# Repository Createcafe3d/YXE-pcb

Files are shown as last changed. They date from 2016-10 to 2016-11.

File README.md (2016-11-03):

Big thanks to Rylan @Peachy for opensourcing the entire project.

Peachy Printer was gearing up to manufacture the mini-v1.14 board. If you're wondering what v1.15 is all about, it's a work-in-progress that we started because of a huge panic: right around the time we were getting ready for our final test manufacturing run, the STM32F042 practically vanished from the entire supply chain! We couldn't find them anywhere! So I quickly started redoing the board to use an STM32F070 instead, but in the end the supply chain recovered before we had to pull the trigger on the respin.

**Todos:**
- Create the trans impedence amplifier for the laser sense pin.
  - This lets us tune the laser power to the "draw velocity" - making for nicer cornering and faster printing
  - The sense pin on the laser is currently grounded (and wrongly labeled as "Laser-EN")

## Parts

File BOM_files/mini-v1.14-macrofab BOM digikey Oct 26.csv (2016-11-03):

Qty | Value | Device | DK P/N | Extended | DK for Ext$ | Package | DK Order Oct 26 | Boards Oct 26
13 | 100n | CAPACITOR_NP_0603 | 399-1095-2-ND | 65000 | 362.7 | C0603 | 4000 | 307
1 | 10uF | CAPACITOR_P_4MM | 490-7201-2-ND | 5000 | 484.35 | CP4MM | 250 | 250
5 | 1uF | C-USC0603 | 311-1443-2-ND | 25000 | 178.25 | C0603 | 4000 | 800
1 | 560pF/50V | C-USC0603 | 1276-1278-2-ND | 5000 | 62.9 | C0603 | 4000 | 4000
1 | BAT42 | DIODE_SOD-123 | BAT42W-FDITR-ND | 5000 | 442.2 | SOD-123 | 120 | 120
4 |  | LEDCHIP-LED0603 | 475-2512-2-ND | 20000 | 1071.2 | CHIP-LED0603 | 1000 | 250
5 | LMC7101 | LMC7101 | 576-2575-2-ND | 25000 | 7725.5 | SOT23-5 | 600 | 120
1 | LMR62014 | LMR62014 | 296-39046-2-ND | 5000 | 2595.55 | SOT23-5 | 120 | 120
1 | ferrite | L-US |  | 5000 |  | C0603 |  | 0
1 | MBR0520 | MBR0520 | MBR0520LT1GOSTR-ND | 5000 | 397.2 | SOD123 | 120 | 120
2 | SMF6.0A | MBR0520 | F5749TR-ND | 10000 | 1517.1 | SOD123 | 250 | 125
2 | NC7WZ14P6X | NC7WZ14P6X | NC7WZ14P6XTR-ND | 10000 | 810.4 | SC70-6 | 250 | 125
2 | BSS138 | N-CHANNEL_FET_SOT-23-3 | BSS138LT3GOSTR-ND | 10000 | 451.64 | SOT-23-3 | 240 | 120
3 |  | PINHD-2X3 | 952-1921-ND | 15000 | 2617.5 | 2X03 | 360 | 120
2 | 10 | RESISTOR_0603 | 311-10.0HRTR-ND | 10000 | 21.26 | R0603 | 5000 | 2500
1 | 100k | RESISTOR_0603 | 311-100KHRTR-ND | 5000 | 9.62 | R0603 | 5000 | 5000
2 | 13k3 | RESISTOR_0603 | 311-13.3KHRTR-ND | 10000 | 21.26 | R0603 | 5000 | 2500
5 | 1k69 | RESISTOR_0603 | 311-1.69KHRTR-ND | 25000 | 47.5 | R0603 | 5000 | 1000
16 | 2k | RESISTOR_0603 | 311-2.00KHRTR-ND | 80000 | 139.2 | R0603 | 5000 | 312
5 | 604k | RESISTOR_0603 | 311-604KHRTR-ND | 25000 | 47.5 | R0603 | 5000 | 1000
1 | 63k4 | RESISTOR_0603 | 311-63.4KHRTR-ND | 5000 | 12.45 | R0603 | 5000 | 5000
10 | 825k | RESISTOR_0603 | 311-825KHRTR-ND | 50000 | 21.62 | R0603 | 5000 | 500
1 | SDR0403-100ML | SDR0403 | SDR0403-100MLTR-ND | 5000 | 1287.25 | SDR0403 | 120 | 120
1 | SP3002-04JTG | SP3002 | F2916TR-ND | 5000 | 1824.75 | SC70-6 | 120 | 120
1 | STM32F070CBT6 | STM32F042-LQFP48 | 497-15099-ND | 5000 | 8179.93 | LQFP48 | 120 | 120
1 | TLV70233PDBVR | TLV70233PDBVR | 296-39284-2-ND | 5000 | 767.64 | SOT-23-5 | 120 | 120
1 |  | USB_MICRO_RIGHT | 609-4618-2-ND | 5000 | 1258.45 | MICROUSB-RIGHT | 120 | 120
TOTAL |  |  |  |  | 32354.92
PER BOARD |  |  |  |  | 6.470984

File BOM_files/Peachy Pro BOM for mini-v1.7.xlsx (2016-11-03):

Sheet: Ordering
Value | Device | Package | Digikey Part | Newark Part Number | Unit Price | /1000 price | QTY | Single Price | Vol Price | QTY +15%
100n | C-USC0603 | C0603 | 399-1095-1-ND |  | 0.13 | 0.00816 | 5 | 0.65 | 0.0408 | 58
10n | C-USC0603 | C0603 | 399-8988-1-ND |  | 0.32 | 0.06934 | 1 | 0.32 | 0.06934 | 12
10uF | C-USC0603 | C0603 | 490-10475-1-ND |  | 0.27 | 0.05056 | 1 | 0.27 | 0.05056 | 12
1u | C-USC0603 | C0603 | 587-1242-1-ND |  | 0.13 | 0.01321 | 3 | 0.39 | 0.03963 | 35
2.2u | C-USC0603 | C0603 | 587-2983-1-ND |  | 0.22 | 0.04095 | 1 | 0.22 | 0.04095 | 12
4.7n | C-USC0603 | C0603 | 399-1087-1-ND |  | 0.13 | 0.00971 | 4 | 0.52 | 0.03884 | 46
470n | C-USC0603 | C0603 | 587-1252-1-ND |  | 0.13 | 0.02136 | 4 | 0.52 | 0.08544 | 46
470p | C-USC0603 | C0603 | 399-1075-1-ND |  | 0.13 | 0.01398 | 1 | 0.13 | 0.01398 | 12
560pF/50V | C-USC0603 | C0603 | 399-1076-1-ND |  | 0.32 | 0.07911 | 1 | 0.32 | 0.07911 | 12
820n | C-USC0603 | C0603 | 399-3117-1-ND |  | 0.34 | 0.08216 | 1 | 0.34 | 0.08216 | 12
BAT60A | BAT60A | SOD323 | BAT60AE6327INCT-ND |  | 0.71 | 0.14888 | 2 | 1.42 | 0.29776 | 23
74S04D | 74S04D | SO14 | 568-1384-1-ND |  | 0.63 | 0.13336 | 1 | 0.63 | 0.13336 | 12
 | LEDCHIP-LED0603 | CHIP-LED0603 | 475-2512-1-ND |  | 0.12 | 0.06086 | 4 | 0.48 | 0.24344 | 46
IRLR3105TR | FET-N-IRLR3105TRIRLR3105TR | DPAK | IRLR3105TRPBFCT-ND |  | 1.48 | 0.5535 | 1 | 1.48 | 0.5535 | 12
1 | R-US_R0603 | R0603 | 541-1.00HHCT-ND |  | 0.112 | 0.02359 | 1 | 0.112 | 0.02359 | 12
100 | R-US_R0603 | R0603 | 541-100HCT-ND |  | 0.112 | 0.02359 | 1 | 0.112 | 0.02359 | 12
100k | R-US_R0603 | R0603 | 541-100KHCT-ND |  | 0.112 | 0.02359 | 1 | 0.112 | 0.02359 | 12
10k | R-US_R0603 | R0603 | 541-10.0KHCT-ND |  | 0.112 | 0.02359 | 1 | 0.112 | 0.02359 | 12
13k3 | R-US_R0603 | R0603 | 541-13.3KHCT-ND |  | 0.112 | 0.02359 | 1 | 0.112 | 0.02359 | 12
1k | R-US_R0603 | R0603 | 541-1.00KHCT-ND |  | 0.112 | 0.02359 | 2 | 0.224 | 0.04718 | 23
1M | R-US_R0603 | R0603 | 541-1.00MHCT-ND |  | 0.112 | 0.02359 | 5 | 0.56 | 0.11795 | 58
3k9 | R-US_R0603 | R0603 | 541-3.90KHCT-ND |  | 0.112 | 0.02359 | 4 | 0.448 | 0.09436 | 46
52k3 | R-US_R0603 | R0603 | 541-52.3KHCT-ND |  | 0.112 | 0.02359 | 1 | 0.112 | 0.02359 | 12
9k9 | R-US_R0603 | R0603 | 541-9.09KHCT-N |  | 0.112 | 0.02359 | 1 | 0.112 | 0.02359 | 12
LD3985M33R | LD3985MXXR | SOT23-5L | 497-3504-1-ND |  | 0.96 | 0.33535 | 1 | 0.96 | 0.33535 | 12
 | R-US_R0603 | R0603 | 541-1.00KHCT-ND |  | 0.112 | 0.02359 | 4 | 0.448 | 0.09436 | 46
FCI-MICRO-USB | FCI-MICRO-USB | FCI-MICROUSB | 609-4613-1-ND |  | 0.6 | 0.3365 | 1 | 0.6 | 0.3365 | 12
LMC7101 | LMC7101 | SOT23-5 | 576-2575-1-ND |  | 0.98 | 0.389 | 4 | 3.92 | 1.556 | 46
LMH6645MF | OPAMP-SINGLELMH6645MF | SOT23-5 | LMH6645MF/NOPBCT-ND |  | 2.49 | 0.97596 | 1 | 2.49 | 0.97596 | 12
LMR62014 | LMR62014 | SOT23-5 | LMR62014XMF/NOPBCT-ND |  | 2.32 | 0.80116 | 1 | 2.32 | 0.80116 | 12
MBR0520 | MBR0520 | SOD123 | MBR0520LT1GOSCT-ND | 48K7498 | 0.407 | 0.076 | 3 | 1.221 | 0.228 | 35
SDR0403-100ML | SDR0403 | SDR0403 | SDR0403-100MLCT-ND |  | 0.65 | 0.31547 | 1 | 0.65 | 0.31547 | 12
SP3002 | SP3002 | SC70-6 | F2916CT-ND |  | 0.96 | 0.38456 | 2 | 1.92 | 0.76912 | 23
STM32F042-LQFP48 | STM32F042-LQFP48 | LQFP48 | 497-14648-ND |  | 4.08 | 2.04112 | 1 | 4.08 | 2.04112 | 12
 | L_TDK_1005 | MLK1005 | 445-1565-1-ND |  | 0.13 | 0.03518 | 1 | 0.13 | 0.03518 | 12
 | NOTE: Replace the existing one with this one (0603)
 |  |  |  |  |  |  | 68 | 28.445 | 9.68171

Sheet: Assembly
Value | QTY | x3
100n | 5 | 15
10n | 1 | 3
10uF | 1 | 3
1u | 3 | 9
2.2u | 1 | 3
4.7n | 4 | 12
470n | 4 | 12
470p | 1 | 3
560pF/50V | 1 | 3
820n | 1 | 3
BAT60A | 2 | 6
74S04D | 1 | 3
 | 4 | 12
IRLR3105TR | 1 | 3
1 | 1 | 3
100 | 1 | 3
100k | 1 | 3
10k | 1 | 3
13k3 | 1 | 3
1k | 2 | 6
1M | 5 | 15
3k9 | 4 | 12
52k3 | 1 | 3
9k9 | 1 | 3
LD3985M33R | 1 | 3
 | 4 | 12
FCI-MICRO-USB | 1 | 3
LMC7101 | 4 | 12
LMH6645MF | 1 | 3
LMR62014 | 1 | 3
MBR0520 | 3 | 9
SDR0403-100ML | 1 | 3
SP3002 | 2 | 6
STM32F042-LQFP48 | 1 | 3
 | 1
 | 68

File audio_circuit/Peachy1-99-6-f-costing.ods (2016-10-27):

Qty | Value | Device | Package | Parts | Description | BOM | DIGIKEY | MF | MPN | Price @500 | Ext @500 | Price @5000 | Ext @5000
1 | 200R | TRIM_US-PVZ3A | PVZ3A | VR5 | POTENTIOMETER |  |  |  | PVZ3G331C01R00 ??? (in stock, not the right one though) | 0.1359 | 0.1359 | 0.12063 | 0.12063
1 | FCI-MICROUSBAPCIRCUITS | FCI-MICROUSBAPCIRCUITS | FCI-USB-10118193-APCIRCUITS | USB2 |  |  |  |  | 10118193-0001LF | 0.31476 | 0.31476 | 0.31476 | 0.31476
1 | LASERDIODELD2 | LASERDIODELD2 | LASERDIODE2 | LD1 |  |  |  |  | 3 x (0552-2-15-15-11-27-10-0) | 0.30582 | 0.30582 | 0.24144 | 0.24144
2 | 10k | TRIM_US-67W | 67W | VR1, VR2 | POTENTIOMETER |  |  |  | 67WR10KLF | 0.64435 | 1.2887 | 0.62981 | 1.25962
1 | ADP1613 | ADP1613 | RM-8 | U1 |  |  |  |  | ADP1613ARMZ-R7 | 1.44978 | 1.44978 | 1.04706 | 1.04706
1 | ADP2300 | ADP2300 | TSOT23-6 | U2 | Nonsynchronous Step-Down Regulator |  |  |  | ADP2300AUJZ-R7 | 1.6776 | 1.6776 | 1.2582 | 1.2582
1 | BC857CT | BC857CT | SC-75 | Q3 |  |  |  |  | BC857CT,115 | 0.0748 | 0.0748 | 0.04457 | 0.04457
1 | MM3ZST1G | MM3ZST1G | SOD323-R | ZD1 |  |  |  |  | BZX384-B3V3,115 | 0.09586 | 0.09586 | 0.05711 | 0.05711
2 | 4.7uF | C-US0805 | C0805 | CIN, CIN-NEG | CAPACITOR, American symbol |  |  |  | CL21A475KOFNNNE | 0.03198 | 0.06396 | 0.02326 | 0.04652
3 | 0.01uF | C-US0805 | C0805 | C4, C6, CSS | CAPACITOR, American symbol |  |  |  | CL21B103KBANNNC | 0.00941 | 0.02823 | 0.00627 | 0.01881
3 | 0.1uF | C-US0805 | C0805 | C1, C2, C3 | CAPACITOR, American symbol |  | 1276-1099-2-ND |  | CL21B104KACNNNC | 0.01344 | 0.04032 | 0.00896 | 0.02688
2 | 0.1uF | C-US0805 | C0805 | C11, CBST-NEG | CAPACITOR, American symbol |  | 1276-1099-2-ND |  | CL21B104KACNNNC | 0.01344 | 0.02688 | 0.00896 | 0.01792
4 | 1uF | C-US0805 | C0805 | C8, C9, CC-NEG, CV5 | CAPACITOR, American symbol |  |  |  | CL21B105KBFNNNE | 0.01802 | 0.07208 | 0.01441 | 0.05764
2 | 10uF | C-US0805 | C0805 | COUT1, COUT1-NEG | CAPACITOR, American symbol |  |  |  | CL21B106KQQNNNE | 0.06856 | 0.13712 | 0.05109 | 0.10218
1 | 6800pF | C-US0805 | C0805 | CC1 | CAPACITOR, American symbol |  |  |  | CL21B682KBANNNC | 0.02016 | 0.02016 | 0.01203 | 0.01203
1 | 10pF | C-US0805 | C0805 | CC2 | CAPACITOR, American symbol |  |  |  | CL21C100JCANNNC | 0.00688 | 0.00688 | 0.0115 | 0.0115
2 | DMG4406LSS | DMG4406LSS | SO8_DMG | Q1, Q2 |  |  |  |  | DMG4406LSS-13 | 0.13099 | 0.26198 | 0.1081 | 0.2162
3 | LM324ADR | LM324ADR | SOIC14(TI-PKG-D) | IC1, IC2, IC3 | OP AMP |  |  |  | LM324ADR | 0.13668 | 0.41004 | 0.10713 | 0.32139
2 | LMC7101 | LMC7101 | SOT23-5 | IC4, IC5 |  |  |  |  | LMC7101BYM5 | 0.36393 | 0.72786 | 0.28075 | 0.5615
1 | 4.7uH | L-USL1210 | L1210 | L1 | INDUCTOR, American symbol |  |  |  | LQH32PN4R7NN0L | 0.28854 | 0.28854 | 0.17212 | 0.17212
1 | 6.8uH | L-USL1210 | L1210 | L1-NEG | INDUCTOR, American symbol |  |  |  | LQH32PN6R8NN0 | 0.28854 | 0.28854 | 0.17212 | 0.17212
4 | RED | LEDCHIPLED_0603 | CHIPLED_0603 | LED1, LED2, LED3, LED4 | LED |  |  |  | LS L29K-G1J2-1-Z | 0.1107 | 0.4428 | 0.09203 | 0.36812
2 | MBR0520 | SCHOTTKYSOD123 | SOD123 | D1-NEG, D3 |  |  |  |  | MBR0520LT3G | 0.07836 | 0.15672 | 0.05065 | 0.1013
1 | MMBT3904 | MMBT3904 | SOT23 | Q4 |  |  |  |  | MMBT3904,215 | 0.03678 | 0.03678 | 0.02069 | 0.02069
1 | OSTTE030104 | OSTTE030104 | OSTTE030104 | X6 |  |  |  |  | OSTTE030104 | 0.35318 | 0.35318 | 0.26488 | 0.26488
1 | 680k* | R-US_SOCKET(.1) | 70543-02 | R28 | RESISTOR, American symbol |  |  |  | PPTC021LFBN-RC | 0.22322 | 0.22322 | 0.15861 | 0.15861
2 | 10k | TRIM_US-PVZ3A | PVZ3A | VR3, VR4 | POTENTIOMETER |  |  |  | PVZ3A103C01R00 | 0.12911 | 0.25822 | 0.08966 | 0.17932
3 | RB751V40 | RB751V40 | SOD323-R | D1, D2, D4 |  |  |  |  | RB751V40,115 | 0.06435 | 0.19305 | 0.04159 | 0.12477
1 | 13k 1% | R-US_R0805 | R0805 | RF2-NEG | RESISTOR, American symbol |  |  |  | RC0805FR-0713KL | 0.00662 | 0.00662 | 0.00319 | 0.00319
2 | 1k37 1% | R-US_R0805 | R0805 | R8, R11 | RESISTOR, American symbol |  |  |  | RC0805FR-071K37L | 0.00489 | 0.00978 | 0.00277 | 0.00554
1 | 1K58 | R-US_R0805 | R0805 | R31 | RESISTOR, American symbol |  |  |  | RC0805FR-071K58L | 0.00662 | 0.00662 | 0.00319 | 0.00319
2 | 2k55 1% | R-US_R0805 | R0805 | R4, R12 | RESISTOR, American symbol |  |  |  | RC0805FR-072K55L | 0.00662 | 0.01324 | 0.00319 | 0.00638
1 | 3k9 1% | R-US_R0805 | R0805 | R13 | RESISTOR, American symbol |  |  |  | RC0805FR-073K9L | 0.00662 | 0.00662 | 0.00319 | 0.00319
1 | 41k2 | R-US_R0805 | R0805 | RF1 | RESISTOR, American symbol |  |  |  | RC0805FR-0741K2L | 0.00662 | 0.00662 | 0.00319 | 0.00319
5 | 6k8 1% | R-US_R0805 | R0805 | R14, R19, R20, R24, R25 | RESISTOR, American symbol |  |  |  | RC0805FR-076K8L | 0.00662 | 0.0331 | 0.00319 | 0.01595
1 | 84k5 1% | R-US_R0805 | R0805 | RF1-NEG | RESISTOR, American symbol |  |  |  | RC0805FR-0784K5L | 0.00662 | 0.00662 | 0.00319 | 0.00319
1 | 300R | R-US_R0805 | R0805 | R7 | RESISTOR, American symbol |  |  |  | RC0805JR-07300RL | 0.00572 | 0.00572 | 0.00274 | 0.00274
1 | 10k7 | R-US_R0805 | R0805 | RF2 | RESISTOR, American symbol |  |  |  | RC2012F1072CS | 0.00648 | 0.00648 | 0.00311 | 0.00311
1 | 1k2 | R-US_R0805 | R0805 | R17 | RESISTOR, American symbol |  |  |  | RC2012J122CS | 0.00562 | 0.00562 | 0.0027 | 0.0027
1 | 2k49 | R-US_R0805 | R0805 | RC1 | RESISTOR, American symbol |  |  |  | RMCF0805FT2K49 | 0.00866 | 0.00866 | 0.00343 | 0.00343
5 | 10k | R-US_R0805 | R0805 | R3, R21, R22, R30, REN | RESISTOR, American symbol |  |  |  | RMCF0805JT10K0 | 0.00348 | 0.0174 | 0.00213 | 0.01065
1 | 1R | R-US_R0805 | R0805 | RB0 | RESISTOR, American symbol |  |  |  | RMCF0805JT1R00 | 0.0062 | 0.0062 | 0.00245 | 0.00245
3 | 20k | R-US_R0805 | R0805 | R9, R10, R29 | RESISTOR, American symbol |  |  |  | RMCF0805JT20K0 | 0.00413 | 0.01239 | 0.00245 | 0.00735
4 | 220R | R-US_R0805 | R0805 | R16, R18, R23, R32 | RESISTOR, American symbol |  |  |  | RMCF0805JT220R | 0.00413 | 0.01652 | 0.00245 | 0.0098
6 | 470k | R-US_R0805 | R0805 | R5, R6, R26, R27, R35, R37 | RESISTOR, American symbol |  |  |  | RMCF0805JT470K | 0.00348 | 0.02088 | 0.00213 | 0.01278
4 | 47k | R-US_R0805 | R0805 | R1, R2, R34, R36 | RESISTOR, American symbol |  | RMCF0805JT47K0CT-ND |  | RMCF0805JT47K0 | 0.00348 | 0.01392 | 0.00213 | 0.00852
1 | 4R7 | R-US_R0805 | R0805 | R15 | RESISTOR, American symbol |  |  |  | RMCF0805JT4R70 | 0.0062 | 0.0062 | 0.00245 | 0.00245
1 | 560R* | R-US_R0805 | R0805 | R33 | RESISTOR, American symbol |  |  |  | RMCF0805JT560R | 0.0062 | 0.0062 | 0.00245 | 0.00245
2 | CUI-SJ-3523-SMT | CUI-SJ-3523-SMT | CUI-SJ-3523-SMT | CON1, CON2 |  |  |  |  | SJ-3523-SMT-TR | 0.62206 | 1.24412 | 0.49571 | 0.99142
2 | TSW-103-02-S-S | TSW-103-02-S-S | TSW-103-02-S-S | X7, X9 | THROUGH-HOLE .025" SQ POST HEADER |  |  |  | TSW-103-07-T-S | 0.30315 | 0.6063 | 0.26591 | 0.53182
3 |  | JUMPER-2SMD-NC | SJ_2S | JP1, JP2, JP3 | Jumper |  |  |  |  |  | 0 |  | 0
1 |  | JUMPER-2SMD-NO | SJ_2S-NO | X5 | Jumper |  |  |  |  |  | 0 |  | 0
2 | FIDUCIAL | FIDUCIAL | FIDUCIAL_1MM | U$2, U$3 | For use by pick and place machines to calibrate the vision/machine, 1mm |  |  |  |  |  | 0 |  | 0
2 | JUMPER-31-2 | JUMPER-31-2 | SJ_3_PASTE1&2 | X2, X3 |  |  |  |  |  |  | 0 |  | 0
1 | SHORT-HT5 | SHORT-HT5 | SHORT_TOP-50 | SH1 | Short between two nets | no |  |  |  |  | 0 |  | 0
15 | TP017HOLE | TP017HOLE | TP017TH | TP7, TP8, TP9, TP12, TP13, TP14, TP15, TP16, TP17, TP18, TP20, TP21, TP22, TP23, TP24 | Test pad |  |  |  |  |  | 0 |  | 0
1 | TP017HOLE | TP017HOLE | TP017TH | TP10 | Test pad |  |  |  |  |  | 0 |  | 0
1 | TP017HOLE | TP017HOLE | TP017TH | TP3 | Test pad |  |  |  |  |  | 0 |  | 0
1 | TP017HOLE | TP017HOLE | TP017TH | TP4 | Test pad |  |  |  |  |  | 0 |  | 0
1 | TP017HOLE | TP017HOLE | TP017TH | TP2 | Test pad |  |  |  |  |  | 0 |  | 0
1 | TP017HOLE | TP017HOLE | TP017TH | TP1 | Test pad |  |  |  |  |  | 0 |  | 0
1 | TP017HOLE | TP017HOLE | TP017TH | TP19 | Test pad |  |  |  |  |  | 0 |  | 0
1 | TP017HOLE | TP017HOLE | TP017TH | TP5 | Test pad |  |  |  |  |  | 0 |  | 0
1 | TP017HOLE | TP017HOLE | TP017TH | TP6 | Test pad |  |  |  |  |  | 0 |  | 0
1 | TP017HOLE | TP017HOLE | TP017TH | TP11 | Test pad |  |  |  |  |  | 0 |  | 0
1 | TSW-102-02-S-S | TSW-102-02-S-S | TSW-102-02-S-S | X10 | THROUGH-HOLE .025" SQ POST HEADER |  |  |  | TSW-102-07-T-S | 0.32538 | 0.32538 | 0.25481 | 0.25481
 |  |  |  |  |  |  |  |  | Totals |  | 11.77099 |  | 9.18819

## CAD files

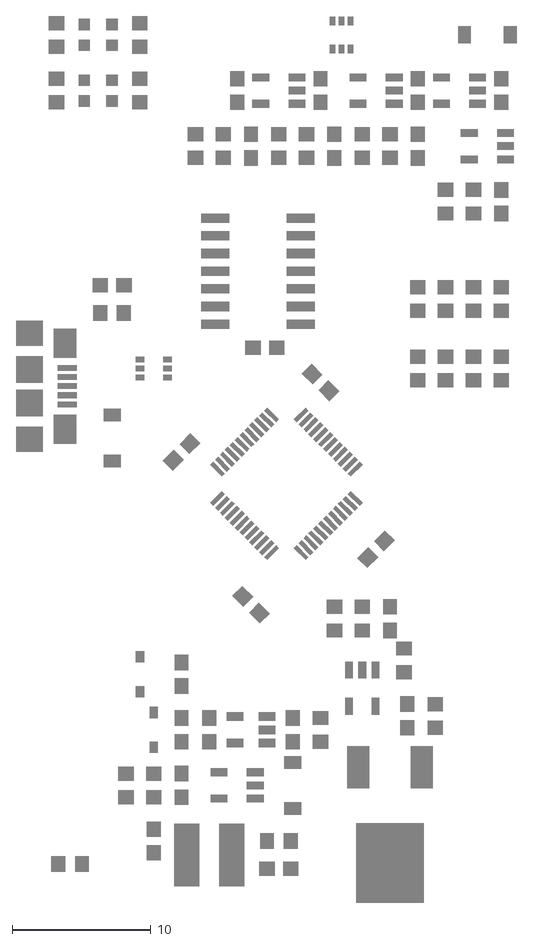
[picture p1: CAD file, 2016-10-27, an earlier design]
old_versions/mini-v1.10-smash-9.dxf
36.0 x 63.8

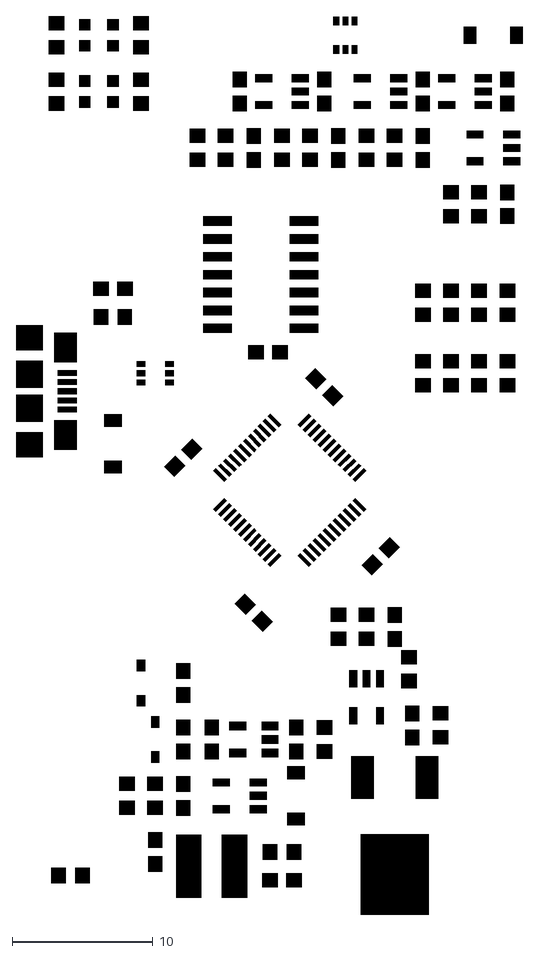
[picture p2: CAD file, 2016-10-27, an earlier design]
old_versions/mini-v1.10-smash-6.dxf
36.0 x 63.8

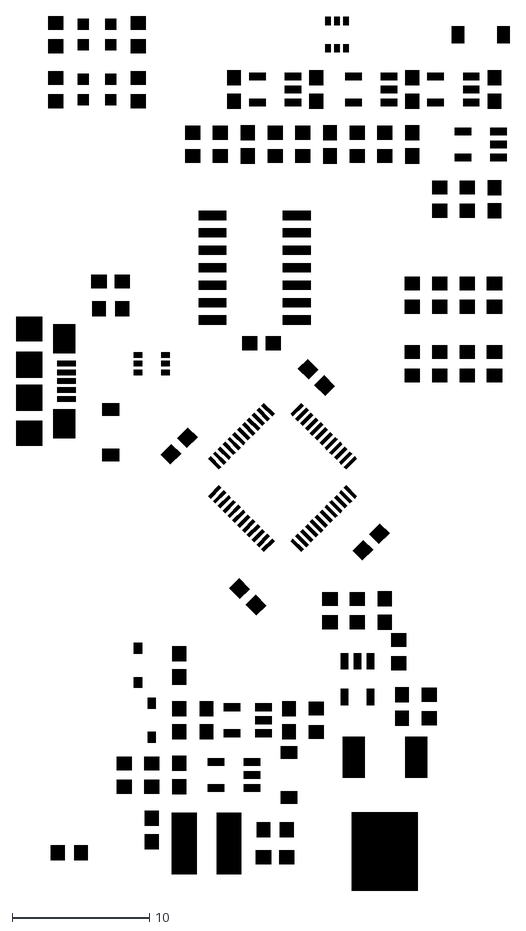
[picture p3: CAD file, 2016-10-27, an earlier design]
old_versions/mini-v1.10-smash-7.dxf
36.0 x 63.8

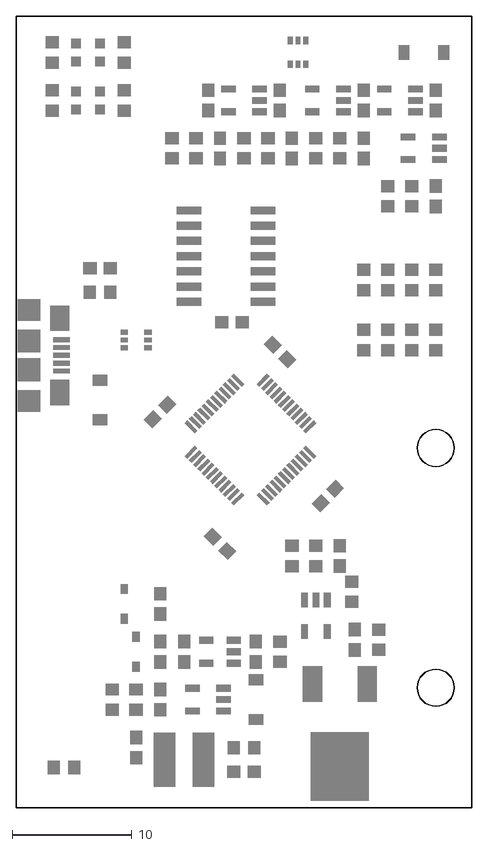
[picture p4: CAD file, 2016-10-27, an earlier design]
old_versions/mini-v1.10-smash.dxf
38.0 x 66.0

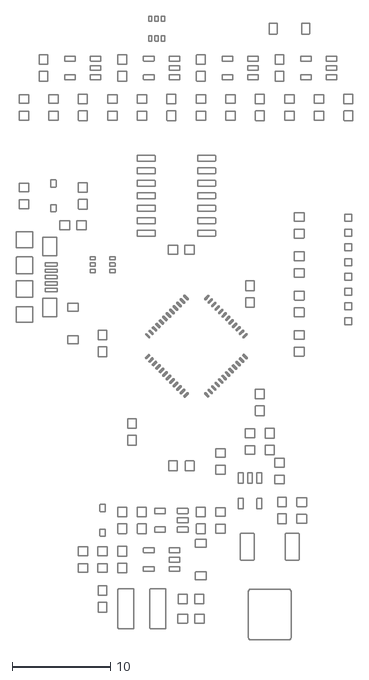
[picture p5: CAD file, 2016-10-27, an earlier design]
old_versions/mini-v1.7-bigger-tcream-tweaked.dxf
34.2 x 63.4

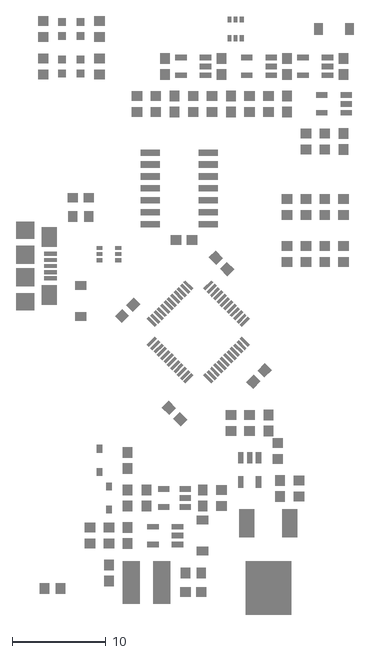
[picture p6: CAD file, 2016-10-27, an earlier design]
old_versions/mini-v1.10-smash-8.dxf
36.0 x 63.8

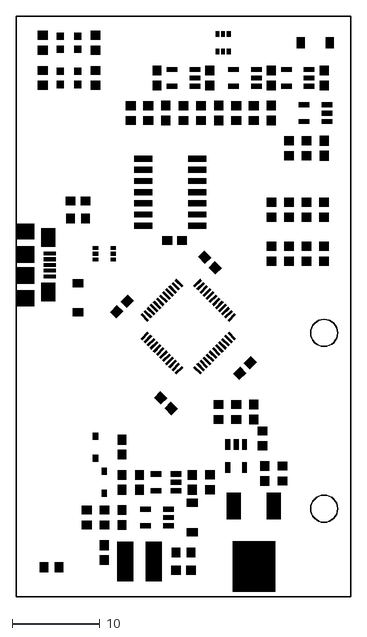
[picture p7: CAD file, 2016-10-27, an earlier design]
old_versions/mini-v1.10-smash-2.dxf
38.0 x 66.0

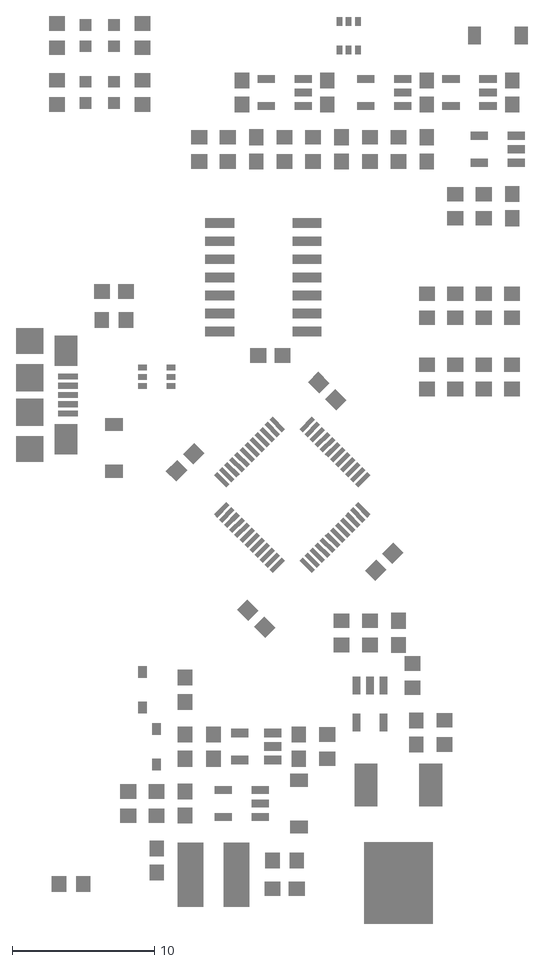
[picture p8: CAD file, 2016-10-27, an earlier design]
old_versions/mini-v1.10-smash-7.1.dxf
36.0 x 63.8

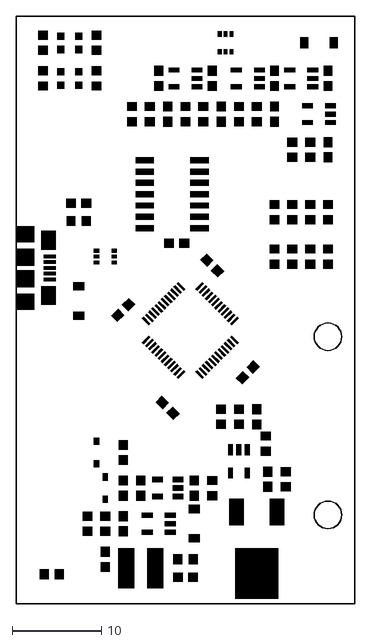
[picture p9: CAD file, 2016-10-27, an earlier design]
old_versions/mini-v1.10-smash-4.dxf
38.0 x 66.0

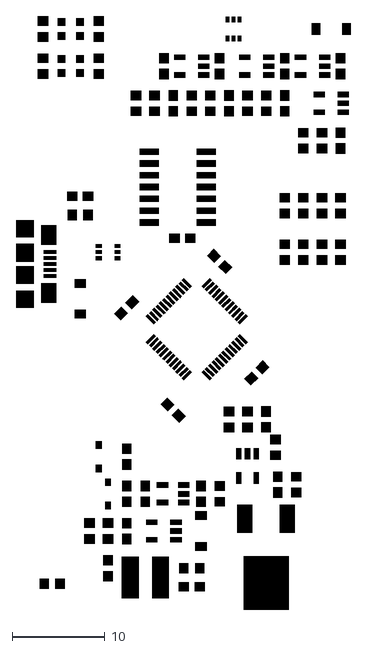
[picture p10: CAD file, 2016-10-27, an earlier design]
old_versions/mini-v1.10-smash-10.dxf
36.0 x 63.8

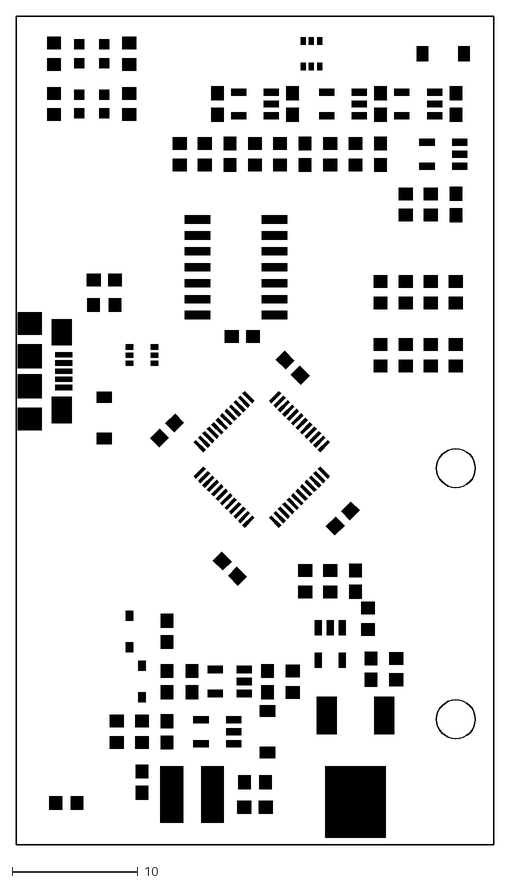
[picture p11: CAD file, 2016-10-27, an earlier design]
old_versions/mini-v1.10-smash-3.dxf
38.0 x 66.0

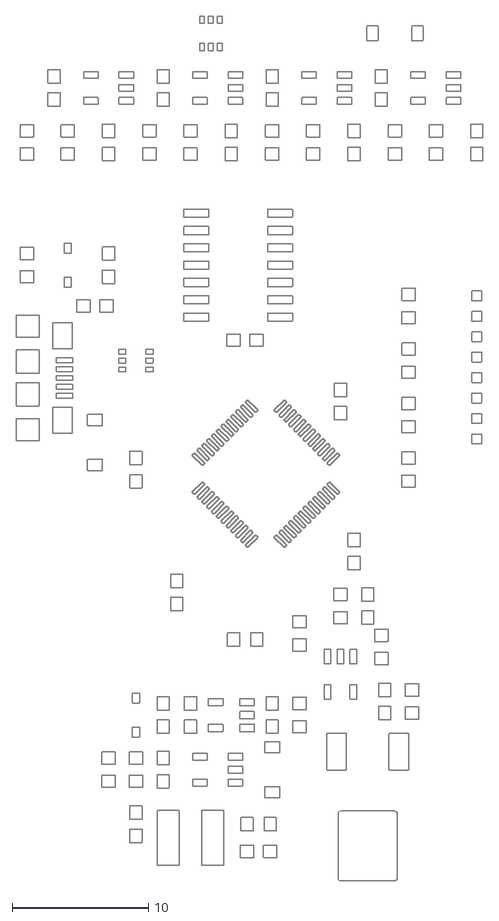
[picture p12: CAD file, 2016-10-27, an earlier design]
old_versions/mini-v1.7-bigger-tcream.dxf
34.2 x 63.4

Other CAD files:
old_versions/mini-v1.10-smash-tcream.dxf
old_versions/mini-v1.10-smash-bcream.dxf
old_versions/mini-v1.10-smash-10.dwg
old_versions/mini-v1.10-smash.dwg

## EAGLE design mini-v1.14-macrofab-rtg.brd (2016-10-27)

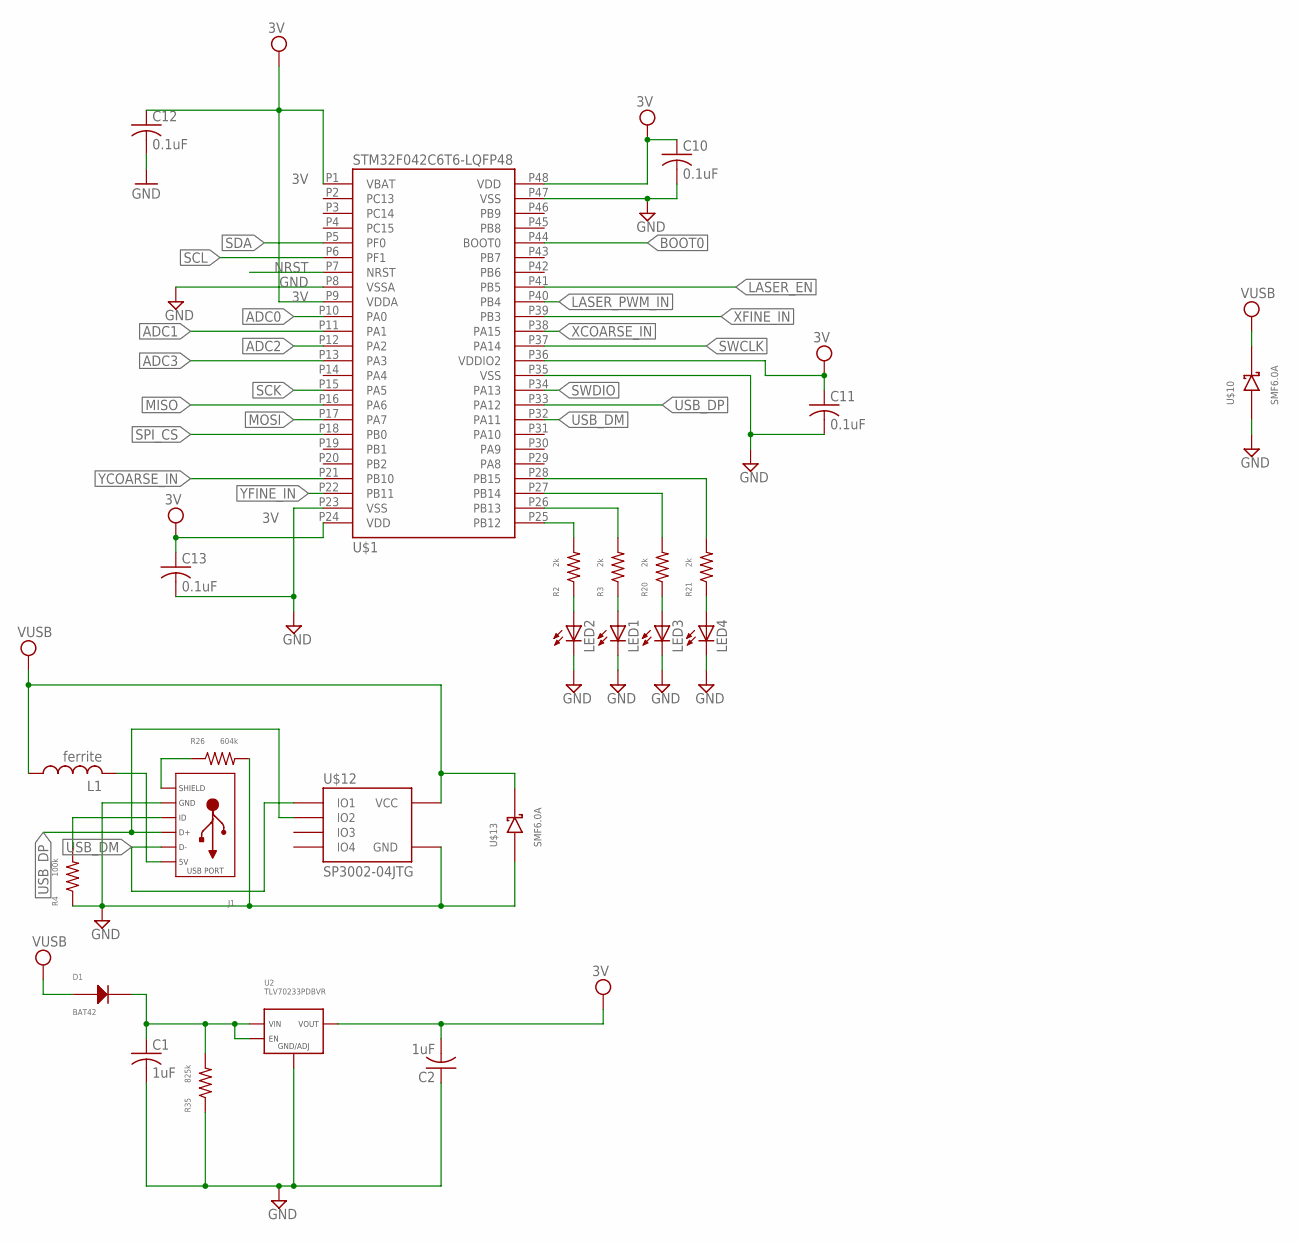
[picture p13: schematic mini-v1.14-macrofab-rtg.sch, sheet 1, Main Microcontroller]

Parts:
C1, C2: 1uF; C0603
C10, C11, C12, C13: 0.1uF; C0603
D1: BAT42; SOD-123
J1: USB_MICRO_RIGHT; MICROUSB-RIGHT
L1: ferrite; C0603
LED1, LED2, LED3, LED4: LEDCHIP-LED0603; CHIP-LED0603
R2, R3, R20, R21: 2k; R0603
R4: 100k; R0603
R26: 604k; R0603
R35: 825k; R0603
U2: TLV70233PDBVR; SOT-23-5
U$1: STM32F042C6T6-LQFP48; LQFP48
U$10, U$13: SMF6.0A; SOD123
U$12: SP3002-04JTG; SC70-6

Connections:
3V: C2.2, C10.1, C11.1, C12.1, C13.1, U2.P$5 (VOUT), U$1.P1 (VBAT), U$1.P9 (VDDA), U$1.P24 (VDD), U$1.P36 (VDDIO2), U$1.P48 (VDD); also elsewhere on the board
ADC0: U$1.P10 (PA0); also elsewhere on the board
ADC1: U$1.P11 (PA1); also elsewhere on the board
ADC2: U$1.P12 (PA2); also elsewhere on the board
ADC3: U$1.P13 (PA3); also elsewhere on the board
BOOT0: U$1.P44 (BOOT0); also elsewhere on the board
GND: C1.2, C2.1, C10.2, C11.2, C12.2, C13.2, J1.5 (GND), LED1.C, LED2.C, LED3.C, LED4.C, R4.P$1, R26.P$2, R35.P$1, U2.P$2 (GND/ADJ), U$1.P8 (VSSA), U$1.P23 (VSS), U$1.P35 (VSS), U$1.P47 (VSS), U$10.ANODE, U$12.P2 (GND), U$13.ANODE; also elsewhere on the board
LASER_EN: U$1.P41 (PB5); also elsewhere on the board
LASER_PWM_IN: U$1.P40 (PB4); also elsewhere on the board
MISO: U$1.P16 (PA6); also elsewhere on the board
MOSI: U$1.P17 (PA7); also elsewhere on the board
unnamed: R2.P$2, U$1.P25 (PB12)
unnamed: LED2.A, R2.P$1
unnamed: C1.1, D1.CATHODE, R35.P$2, U2.P$1 (VIN), U2.P$3 (EN)
unnamed: J1.4 (ID), R4.P$2
unnamed: LED1.A, R3.P$1
unnamed: R3.P$2, U$1.P26 (PB13)
unnamed: J1.1 (5V), L1.2
unnamed: J1.S1 (SLD), J1.S2 (SLD), J1.S3 (SLD), J1.S4 (SLD), J1.S5 (SLD), J1.S6 (SLD), R26.P$1
unnamed: LED3.A, R20.P$1
unnamed: LED4.A, R21.P$1
unnamed: R20.P$2, U$1.P27 (PB14)
unnamed: R21.P$2, U$1.P28 (PB15)
NRST: U$1.P7 (NRST); also elsewhere on the board
SCK: U$1.P15 (PA5); also elsewhere on the board
SCL: U$1.P6 (PF1); also elsewhere on the board
SDA: U$1.P5 (PF0); also elsewhere on the board
SPI_CS: U$1.P18 (PB0); also elsewhere on the board
SWCLK: U$1.P37 (PA14); also elsewhere on the board
SWDIO: U$1.P34 (PA13); also elsewhere on the board
USB_DM: J1.2 (D-), U$1.P32 (PA11), U$12.P1 (IO1)
USB_DP: J1.3 (D+), U$1.P33 (PA12), U$12.P3 (IO2)
VUSB: D1.ANODE, L1.1, U$10.CATHODE, U$12.P5 (VCC), U$13.CATHODE; also elsewhere on the board
XCOARSE_IN: U$1.P38 (PA15); also elsewhere on the board
XFINE_IN: U$1.P39 (PB3); also elsewhere on the board
YCOARSE_IN: U$1.P21 (PB10); also elsewhere on the board
YFINE_IN: U$1.P22 (PB11); also elsewhere on the board

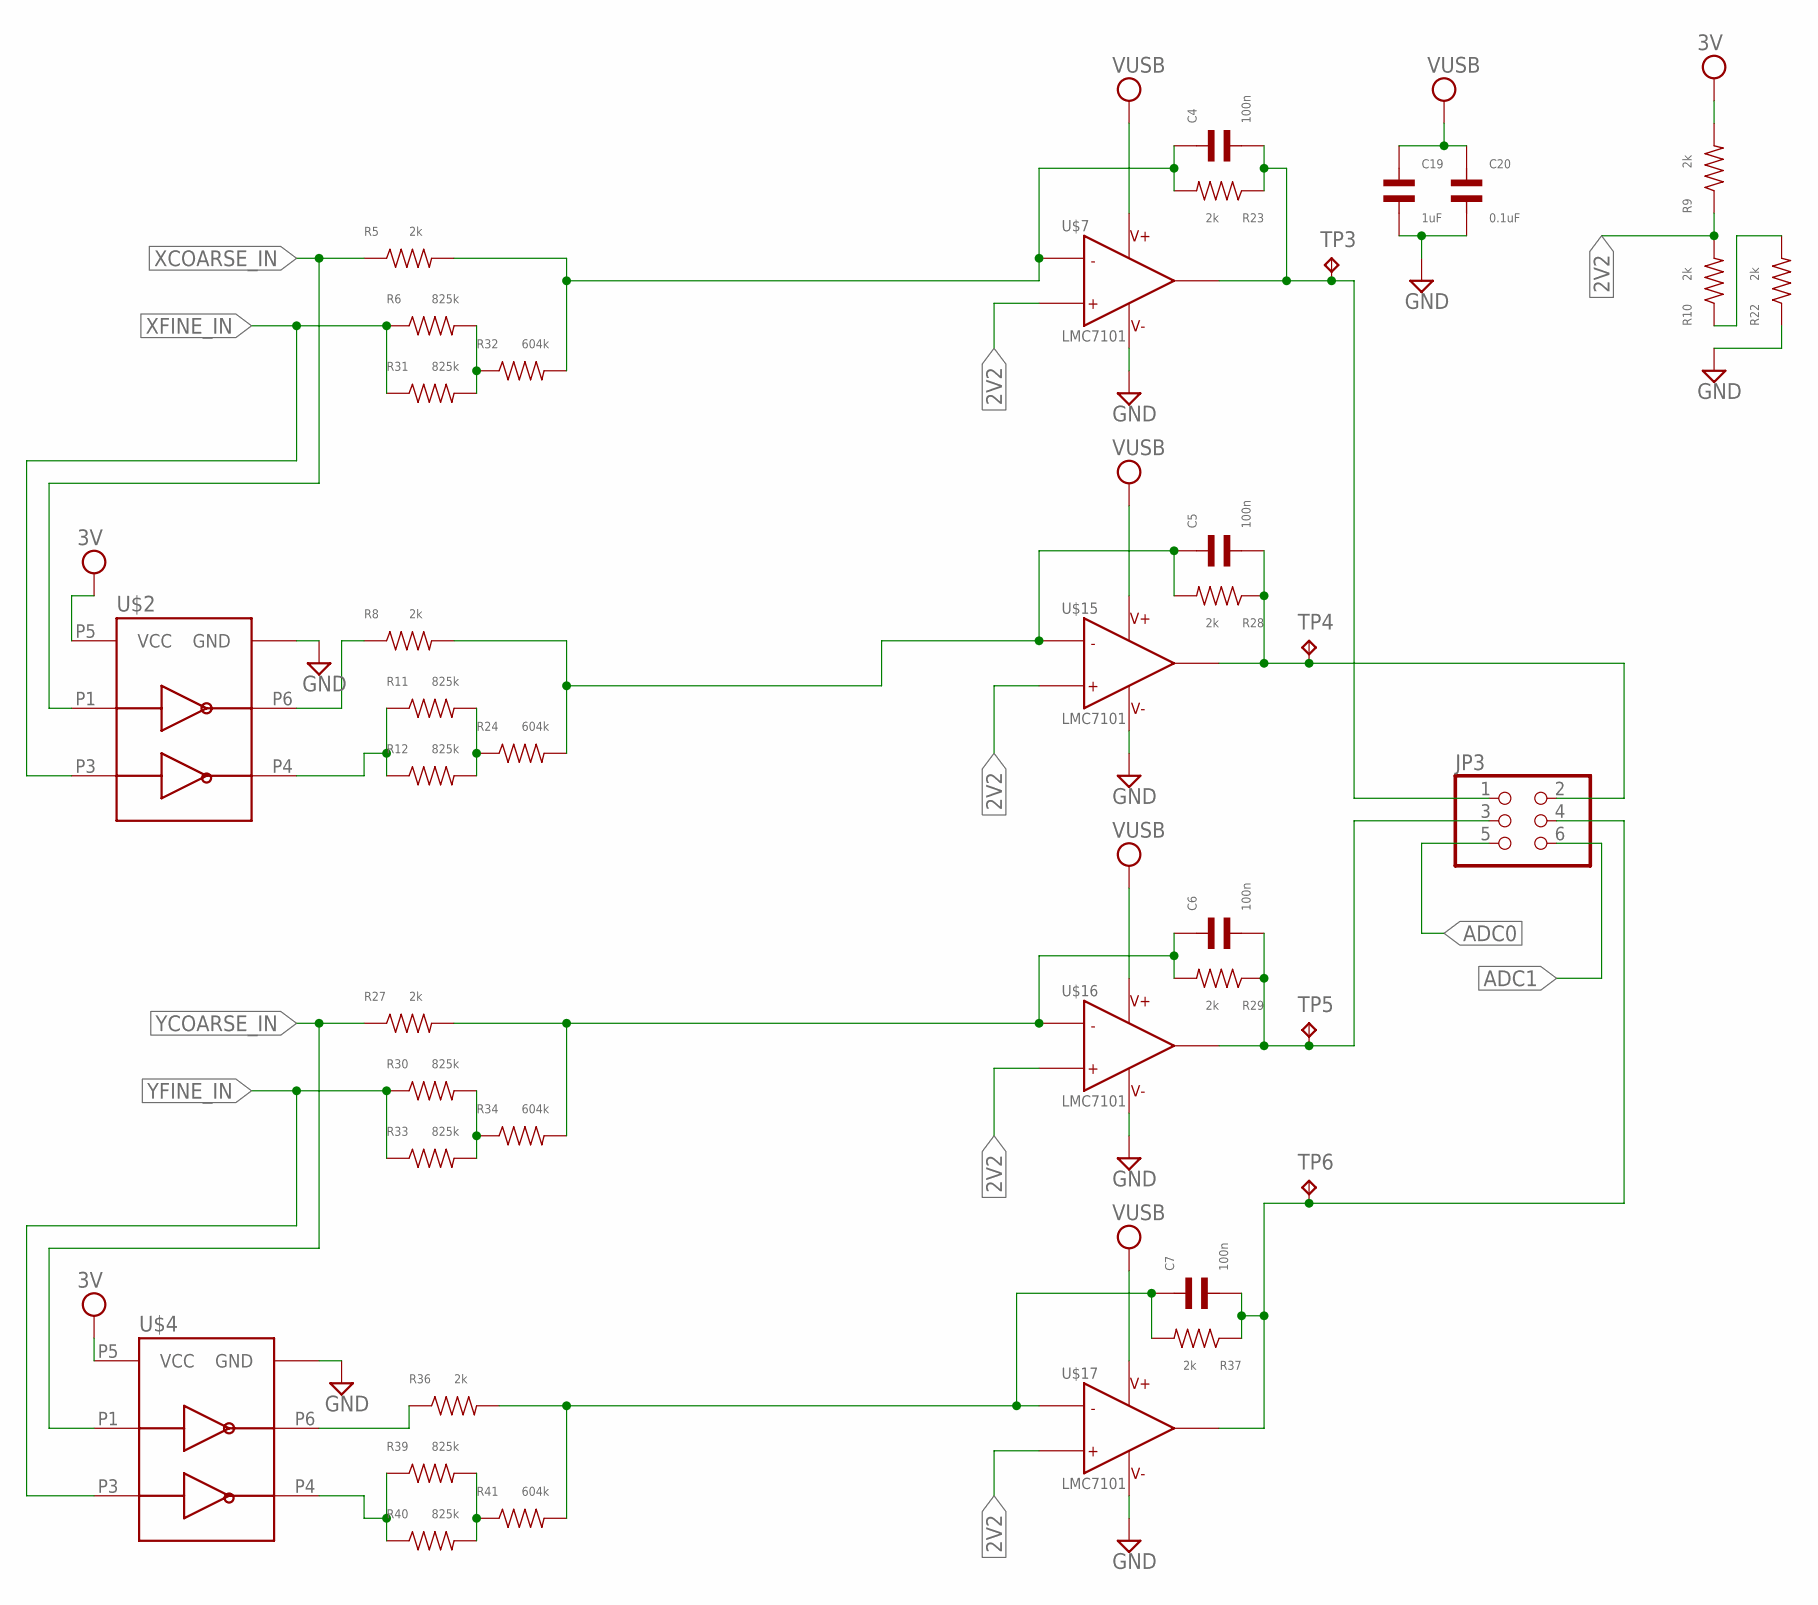
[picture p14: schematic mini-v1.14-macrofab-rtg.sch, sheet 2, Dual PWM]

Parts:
C4, C5, C6, C7: 100n; C0603
C19: 1uF; C0603
C20: 0.1uF; C0603
JP3: PINHD-2X3; 2X03
R5, R8, R9, R10, R22, R23, R27, R28, R29, R36, R37: 2k; R0603
R6, R11, R12, R30, R31, R33, R39, R40: 825k; R0603
R24, R32, R34, R41: 604k; R0603
TP3, TP4, TP5, TP6: TPB1,27; B1,27
U$2, U$4: NC7WZ14P6X; SC70-6
U$7, U$15, U$16, U$17: LMC7101; SOT23-5

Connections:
2V2: R9.P$1, R10.P$2, U$7.3, U$15.3, U$16.3, U$17.3
3V: R9.P$2, U$2.P5 (VCC), U$4.P5 (VCC); also elsewhere on the board
ADC0: JP3.5; also elsewhere on the board
ADC1: JP3.6; also elsewhere on the board
COARSE1: R8.P$1, U$2.P6 (Y1)
FINE1: R11.P$1, R12.P$1, U$2.P4 (Y2)
FINE3: R39.P$1, R40.P$1, U$4.P4 (Y2)
GND: C19.P$2, C20.P$2, R22.P$1, U$2.P2 (GND), U$4.P2 (GND), U$7.5, U$15.5, U$16.5, U$17.5; also elsewhere on the board
unnamed: R36.P$1, U$4.P6 (Y1)
unnamed: R11.P$2, R12.P$2, R24.P$1
unnamed: C5.P$1, R8.P$2, R24.P$2, R28.P$2, U$15.4
unnamed: R10.P$1, R22.P$2
unnamed: R30.P$2, R33.P$2, R34.P$1
unnamed: R6.P$2, R31.P$2, R32.P$1
unnamed: C6.P$1, R27.P$2, R29.P$2, R34.P$2, U$16.4
unnamed: R39.P$2, R40.P$2, R41.P$1
unnamed: C7.P$1, R36.P$2, R37.P$2, R41.P$2, U$17.4
OUT: C4.P$2, JP3.1, R23.P$1, TP3.TP, U$7.1
OUT1: C5.P$2, JP3.2, R28.P$1, TP4.TP, U$15.1
OUT2: C6.P$2, JP3.3, R29.P$1, TP5.TP, U$16.1
OUT3: C7.P$2, JP3.4, R37.P$1, TP6.TP, U$17.1
VUSB: C19.P$1, C20.P$1, U$7.2, U$15.2, U$16.2, U$17.2; also elsewhere on the board
XCOARSE_IN: R5.P$1, U$2.P1 (A1); also elsewhere on the board
XFINE_IN: R6.P$1, R31.P$1, U$2.P3 (A2); also elsewhere on the board
XSUM: C4.P$1, R5.P$2, R23.P$2, R32.P$2, U$7.4
YCOARSE_IN: R27.P$1, U$4.P1 (A1); also elsewhere on the board
YFINE_IN: R30.P$1, R33.P$1, U$4.P3 (A2); also elsewhere on the board

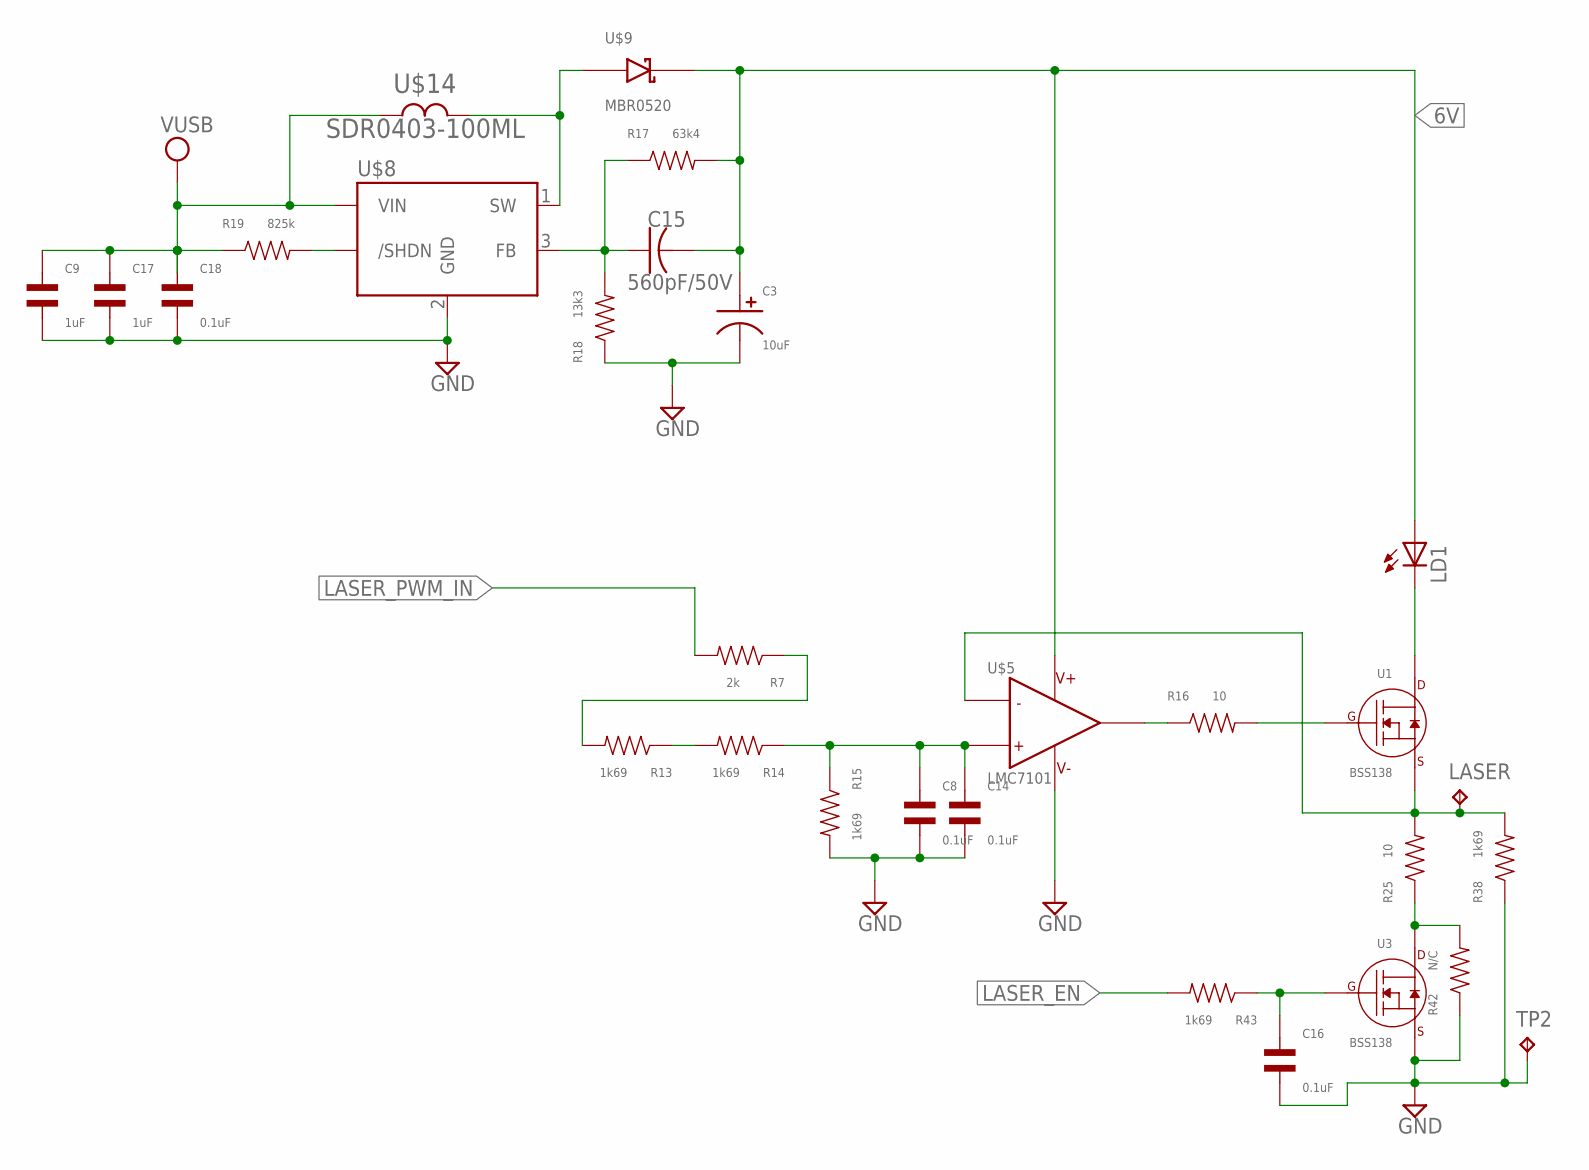
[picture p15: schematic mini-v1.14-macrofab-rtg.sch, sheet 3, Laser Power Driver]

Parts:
C3: 10uF; CP4MM
C8, C14, C16, C18: 0.1uF; C0603
C9, C17: 1uF; C0603
C15: 560pF/50V; C0603
LASER: TPB2,54; B2,54
LD1: SCOTT_LASERDIODELD3; SCOTT_LASERDIODE3; MPN 3 x (0552-2-15-15-11-27-10-0)
R7: 2k; R0603
R13, R14, R15, R38, R43: 1k69; R0603
R16, R25: 10; R0603
R17: 63k4; R0603
R18: 13k3; R0603
R19: 825k; R0603
R42: N/C; R0603
TP2: GND; B2,54
U1, U3: BSS138; SOT-23-3
U$5: LMC7101; SOT23-5
U$8: LMR62014; SOT23-5
U$9: MBR0520; SOD123
U$14: SDR0403-100ML; SDR0403

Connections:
6V: C3.P$1, C15.2, LD1.P$1 (A), R17.P$2, U$5.2 (V+), U$9.CATHODE
GND: C3.P$2, C8.P$2, C9.P$2, C14.P$2, C16.P$2, C17.P$2, C18.P$2, R15.P$2, R18.P$1, R38.P$1, R42.P$1, TP2.TP, U3.P$2 (SOURCE), U$5.5 (V-), U$8.2 (GND); also elsewhere on the board
LASER_EN: R43.P$2; also elsewhere on the board
LASER_PWM_IN: R7.P$2; also elsewhere on the board
unnamed: R25.P$1, R42.P$2, U3.P$3 (DRAIN)
unnamed: R7.P$1, R13.P$2
unnamed: R13.P$1, R14.P$2
unnamed: C8.P$1, C14.P$1, R14.P$1, R15.P$1, U$5.3 (IN+)
unnamed: U$8.1 (SW), U$9.ANODE, U$14.P$2
unnamed: LD1.P$3 (C), U1.P$3 (DRAIN)
unnamed: LASER.TP, R25.P$2, R38.P$2, U1.P$2 (SOURCE), U$5.4 (IN-)
unnamed: R16.P$2, U1.P$1 (GATE)
unnamed: R16.P$1, U$5.1 (OUT)
unnamed: C16.P$1, R43.P$1, U3.P$1 (GATE)
unnamed: C15.1, R17.P$1, R18.P$2, U$8.3 (FB)
unnamed: R19.P$2, U$8.4 (/SHDN)
VUSB: C9.P$1, C17.P$1, C18.P$1, R19.P$1, U$8.5 (VIN), U$14.P$1; also elsewhere on the board

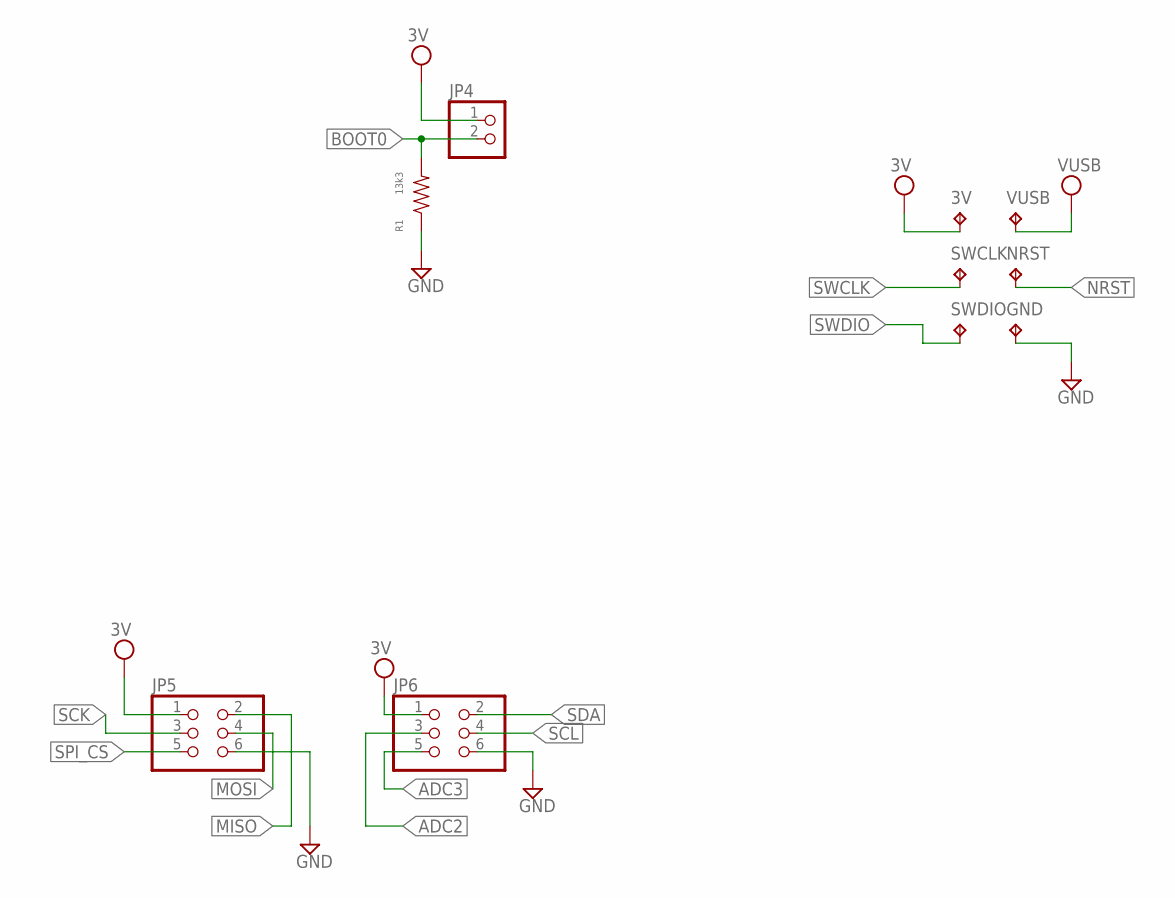
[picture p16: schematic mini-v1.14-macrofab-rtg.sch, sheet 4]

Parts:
3V: TPB1,27; B1,27
GND: TPB1,27; B1,27
JP4: PINHD-1X2; 1X02
JP5, JP6: PINHD-2X3; 2X03
NRST: TPB1,27; B1,27
R1: 13k3; R0603
SWCLK: TPB1,27; B1,27
SWDIO: TPB1,27; B1,27
VUSB: TPB1,27; B1,27

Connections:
3V: 3V.TP, JP4.1, JP5.1, JP6.1; also elsewhere on the board
ADC2: JP6.3; also elsewhere on the board
ADC3: JP6.5; also elsewhere on the board
BOOT0: JP4.2, R1.P$2; also elsewhere on the board
GND: GND.TP, JP5.6, JP6.6, R1.P$1; also elsewhere on the board
MISO: JP5.2; also elsewhere on the board
MOSI: JP5.4; also elsewhere on the board
NRST: NRST.TP; also elsewhere on the board
SCK: JP5.3; also elsewhere on the board
SCL: JP6.4; also elsewhere on the board
SDA: JP6.2; also elsewhere on the board
SPI_CS: JP5.5; also elsewhere on the board
SWCLK: SWCLK.TP; also elsewhere on the board
SWDIO: SWDIO.TP; also elsewhere on the board
VUSB: VUSB.TP; also elsewhere on the board

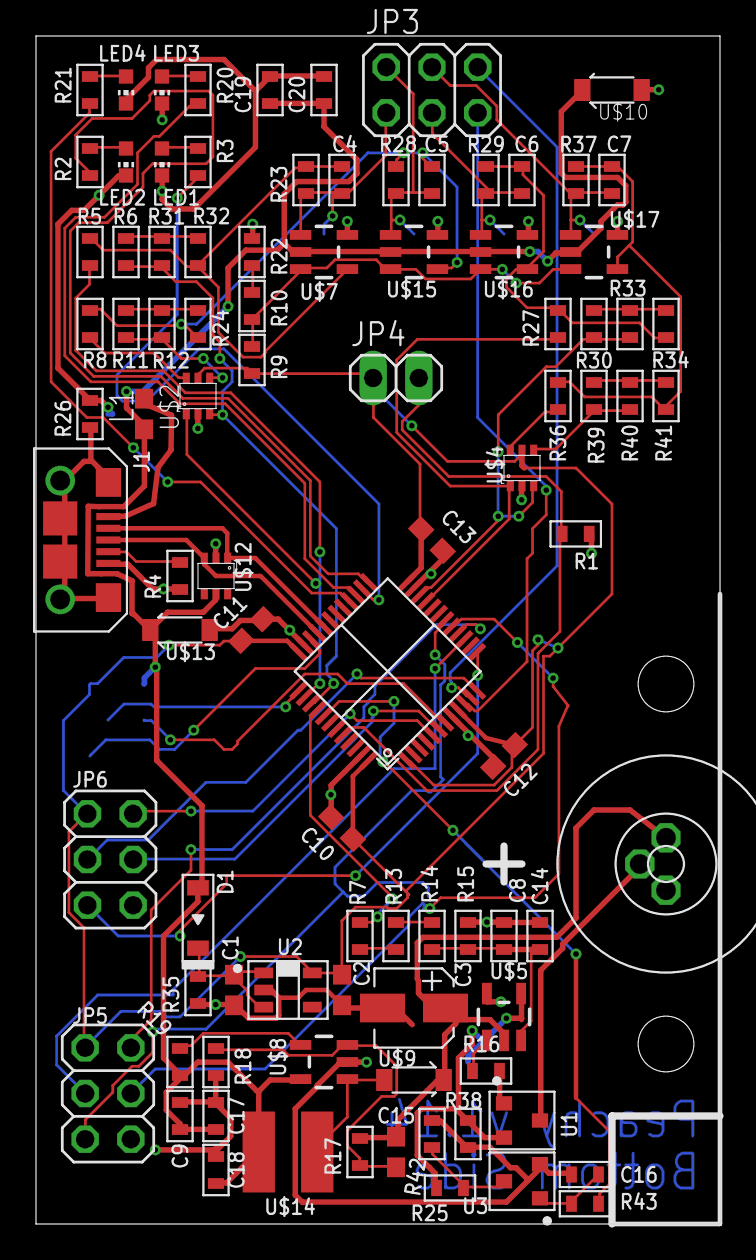
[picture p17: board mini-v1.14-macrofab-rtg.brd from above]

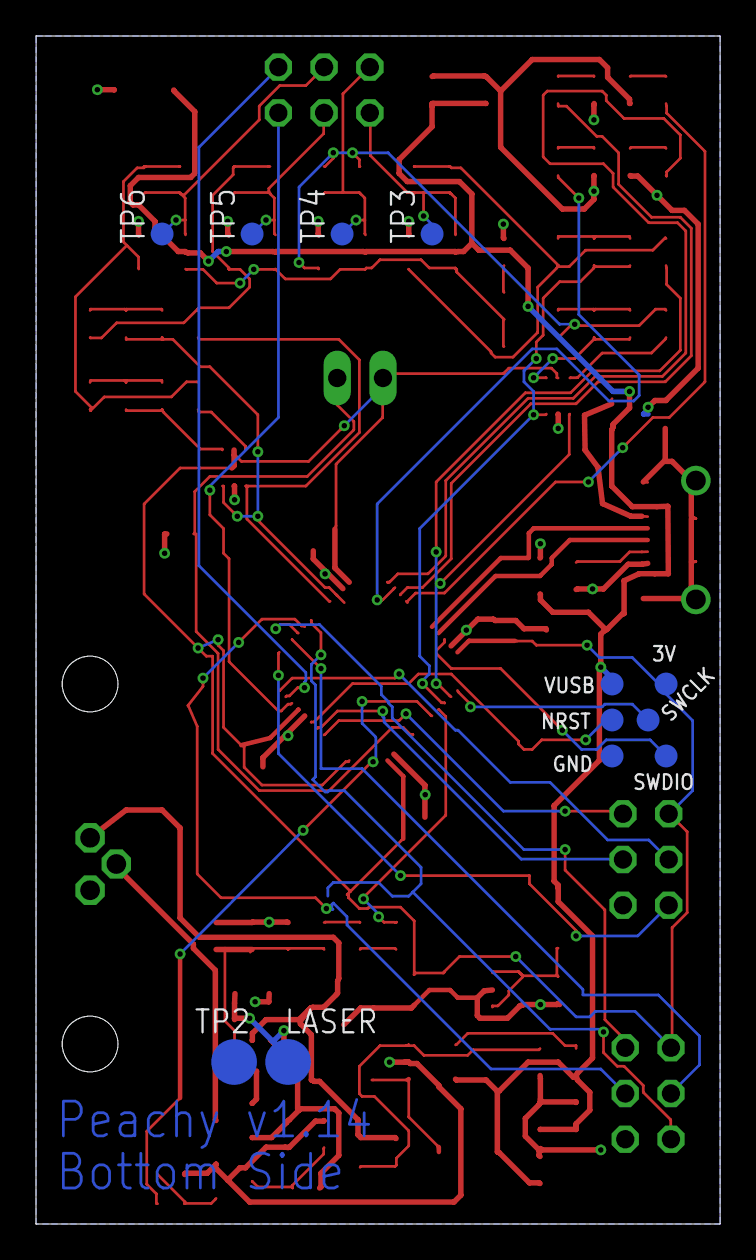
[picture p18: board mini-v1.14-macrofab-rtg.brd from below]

Board: 2 copper layers, 38.0 x 66.0 mm, 104 parts (12 on the bottom side), 68 nets.

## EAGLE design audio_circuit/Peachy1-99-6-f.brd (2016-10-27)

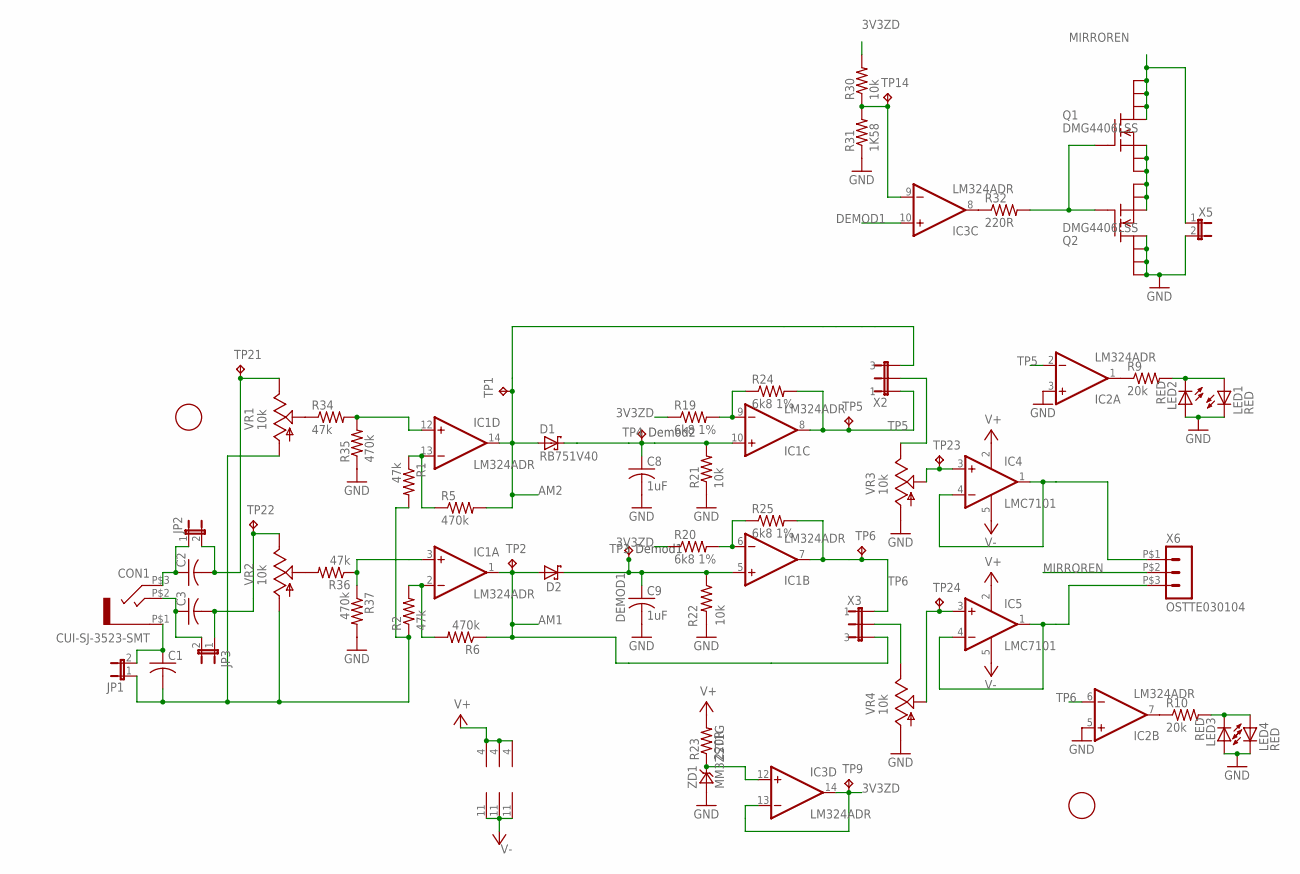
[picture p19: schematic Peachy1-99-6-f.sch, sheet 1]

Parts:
C1, C2, C3: C-US0805; C0805
C8, C9: 1uF; C0805; MPN CL21B105KBFNNNE
CON1: CUI-SJ-3523-SMT; MPN SJ-3523-SMT-TR
D1, D2: RB751V40; SOD323-R; MPN RB751V40,115
IC1, IC2, IC3: LM324ADR; SOIC14(TI-PKG-D); MPN LM324ADR
IC4, IC5: LMC7101; SOT23-5; MPN LMC7101BYM5
JP1, JP2, JP3: JUMPER-2SMD-NC; SJ_2S
LED1, LED2, LED3, LED4: RED; CHIPLED_0603; MPN LS L29K-G1J2-1-Z
Q1, Q2: DMG4406LSS; SO8_DMG; MPN DMG4406LSS-13
R1, R2, R34, R36: 47k; R0805; MPN RMCF0805JT47K0; DIGIKEY RMCF0805JT47K0CT-ND
R5, R6, R35, R37: 470k; R0805; MPN RMCF0805JT470K
R9, R10: 20k; R0805; MPN RMCF0805JT20K0
R19, R20, R24, R25: 6k8 1%; R0805; MPN RC0805FR-076K8L
R21, R22, R30: 10k; R0805; MPN RMCF0805JT10K0
R23, R32: 220R; R0805; MPN RMCF0805JT220R
R31: 1K58; R0805; MPN RC0805FR-071K58L
TP1, TP2, TP3, TP4, TP5, TP6, TP9, TP14, TP21, TP22, TP23, TP24: TP017HOLE; TP017TH
U$2, U$3: FIDUCIAL; FIDUCIAL_1MM
VR1, VR2: 10k; 67W; MPN 67WR10KLF
VR3, VR4: 10k; PVZ3A; MPN PVZ3A103C01R00
X2, X3: JUMPER-31-2; SJ_3_PASTE1&2
X5: JUMPER-2SMD-NO; SJ_2S-NO
X6: OSTTE030104; MPN OSTTE030104
ZD1: MM3ZST1G; SOD323-R; MPN BZX384-B3V3,115

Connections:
3V3ZD: IC3.13 (-IN), IC3.14 (OUT), R19.1, R20.1, R30.2, TP9.P$1; also elsewhere on the board
AM1: D2.A, IC1.1 (OUT), R6.1, TP2.P$1, X3.3; also elsewhere on the board
AM2: D1.A, IC1.14 (OUT), R5.2, TP1.P$1, X2.3
DEMOD1: C9.1, D2.C, IC1.5 (+IN), IC3.10 (+IN), R22.1, TP3.P$1
DEMOD2: C8.1, D1.C, IC1.10 (+IN), R21.2, TP4.P$1
GND: C8.2, C9.2, IC2.3 (+IN), IC2.5 (+IN), LED1.C, LED2.A, LED3.A, LED4.C, Q2.P$5 (D), Q2.P$6 (D), Q2.P$7 (D), Q2.P$8 (D), R21.1, R22.2, R31.1, R35.1, R37.2, VR3.P$1 (A), VR4.P$1 (A), X5.2, ZD1.A; also elsewhere on the board
MIRROREN: Q1.P$5 (D), Q1.P$6 (D), Q1.P$7 (D), Q1.P$8 (D), X5.1, X6.P$2 (2)
unnamed: C3.2, JP3.1, TP22.P$1, VR2.E
unnamed: C1.2, JP1.1, R1.2, R2.1, VR1.A, VR2.A
unnamed: R34.1, VR1.S
unnamed: IC1.13 (-IN), R1.1, R5.1
unnamed: IC1.12 (+IN), R34.2, R35.2
unnamed: VR4.P$3 (E), X3.2
unnamed: IC3.12 (+IN), R23.1, ZD1.C
unnamed: IC1.2 (-IN), R2.2, R6.2
unnamed: IC4.3 (+IN), TP23.P$1, VR3.P$2 (S)
unnamed: R36.2, VR2.S
unnamed: IC1.3 (+IN), R36.1, R37.1
unnamed: IC1.9 (-IN), R19.2, R24.1
unnamed: IC2.1 (OUT), R9.1
unnamed: IC1.6 (-IN), R20.2, R25.1
unnamed: IC2.7 (OUT), R10.1
unnamed: IC5.1 (OUT), IC5.4 (-IN), X6.P$3 (3)
unnamed: IC4.1 (OUT), IC4.4 (-IN), X6.P$1 (1)
unnamed: VR3.P$3 (E), X2.2
unnamed: IC5.3 (+IN), TP24.P$1, VR4.P$2 (S)
unnamed: Q1.P$4 (G), Q2.P$4 (G), R32.2
unnamed: Q1.P$1 (S), Q1.P$2 (S), Q1.P$3 (S), Q2.P$1 (S), Q2.P$2 (S), Q2.P$3 (S)
unnamed: IC3.9 (-IN), R30.1, R31.2, TP14.P$1
unnamed: LED1.A, LED2.C, R9.2
unnamed: IC3.8 (OUT), R32.1
unnamed: LED3.C, LED4.A, R10.2
unnamed: C1.1, CON1.P$1 (1), JP1.2
unnamed: C3.1, CON1.P$2 (3), JP3.2
unnamed: C2.1, CON1.P$3 (2), JP2.1
unnamed: C2.2, JP2.2, TP21.P$1, VR1.E
TP5: IC1.8 (OUT), IC2.2 (-IN), R24.2, TP5.P$1, X2.1
TP6: IC1.7 (OUT), IC2.6 (-IN), R25.2, TP6.P$1, X3.1
V+: IC1.4 (V+), IC2.4 (V+), IC3.4 (V+), IC4.2 (V+), IC5.2 (V+), R23.2; also elsewhere on the board
V-: IC1.11 (V-), IC2.11 (V-), IC3.11 (V-), IC4.5 (V-), IC5.5 (V-); also elsewhere on the board

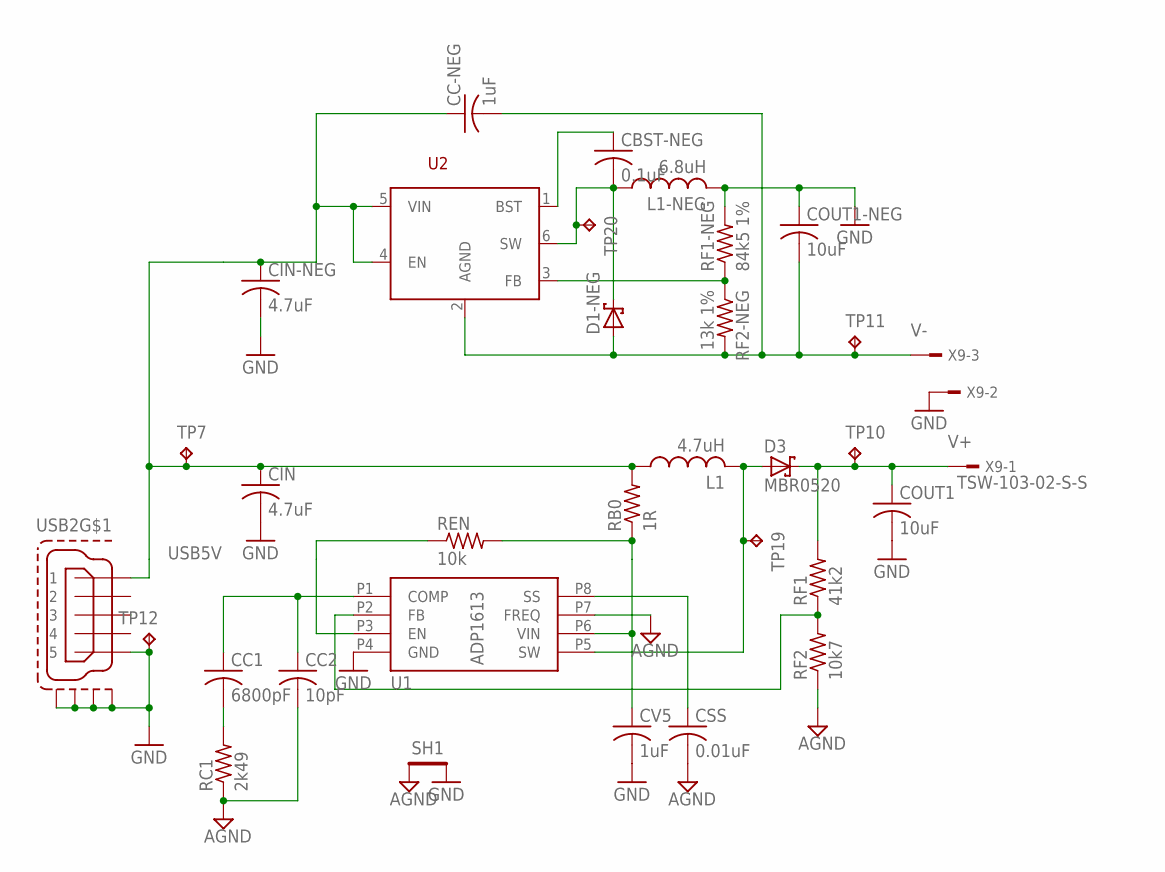
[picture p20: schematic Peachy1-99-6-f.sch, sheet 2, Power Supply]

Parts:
CBST-NEG: 0.1uF; C0805; MPN CL21B104KACNNNC
CC1: 6800pF; C0805; MPN CL21B682KBANNNC
CC2: 10pF; C0805; MPN CL21C100JCANNNC
CC-NEG: 1uF; C0805; MPN CL21B105KBFNNNE
CIN: 4.7uF; C0805; MPN CL21A475KOFNNNE
CIN-NEG: 4.7uF; C0805; MPN CL21A475KOFNNNE
COUT1, COUT1-NEG: 10uF; C0805; MPN CL21B106KQQNNNE
CSS: 0.01uF; C0805; MPN CL21B103KBANNNC
CV5: 1uF; C0805; MPN CL21B105KBFNNNE
D1-NEG, D3: MBR0520; SOD123; MPN MBR0520LT3G
L1: 4.7uH; L1210; MPN LQH32PN4R7NN0L
L1-NEG: 6.8uH; L1210; MPN LQH32PN6R8NN0
RB0: 1R; R0805; MPN RMCF0805JT1R00
RC1: 2k49; R0805; MPN RMCF0805FT2K49
REN: 10k; R0805; MPN RMCF0805JT10K0
RF1: 41k2; R0805; MPN RC0805FR-0741K2L
RF1-NEG: 84k5 1%; R0805; MPN RC0805FR-0784K5L
RF2: 10k7; R0805; MPN RC2012F1072CS
RF2-NEG: 13k 1%; R0805; MPN RC0805FR-0713KL
SH1: SHORT-HT5; SHORT_TOP-50
TP7, TP10, TP11, TP12, TP19, TP20: TP017HOLE; TP017TH
U1: ADP1613; RM-8; MPN ADP1613ARMZ-R7
U2: ADP2300; TSOT23-6; MPN ADP2300AUJZ-R7
USB2: FCI-MICROUSBAPCIRCUITS; FCI-USB-10118193-APCIRCUITS; MPN 10118193-0001LF
X9: TSW-103-02-S-S; MPN TSW-103-07-T-S

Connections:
AGND: CC2.2, CSS.2, RC1.1, RF2.1, SH1.1, U1.P7 (FREQ)
BOOST: CBST-NEG.1, U2.1 (BST)
GND: CIN.2, CIN-NEG.2, COUT1.2, COUT1-NEG.1, CV5.2, L1-NEG.2, RF1-NEG.2, SH1.2, TP12.P$1, U1.P4 (GND), USB2.P$5 (5), USB2.P$6 (S1), USB2.P$7 (S2), USB2.P$8 (S3), USB2.P$11 (S4), X9.2; also elsewhere on the board
unnamed: CV5.1, RB0.1, REN.2, U1.P6 (VIN)
unnamed: REN.1, U1.P3 (EN)
unnamed: CSS.1, U1.P8 (SS)
unnamed: RF1.1, RF2.2, U1.P2 (FB)
unnamed: CC1.1, CC2.1, U1.P1 (COMP)
unnamed: CC1.2, RC1.2
unnamed: RF1-NEG.1, RF2-NEG.1, U2.3 (FB)
SW+: D3.A, L1.2, TP19.P$1, U1.P5 (SW)
SW-: CBST-NEG.2, D1-NEG.C, L1-NEG.1, TP20.P$1, U2.6 (SW)
USB5V: CC-NEG.1, CIN.1, CIN-NEG.1, L1.1, RB0.2, TP7.P$1, U2.4 (EN), U2.5 (VIN), USB2.P$1 (1)
V+: COUT1.1, D3.C, RF1.2, TP10.P$1, X9.1; also elsewhere on the board
V-: CC-NEG.2, COUT1-NEG.2, D1-NEG.A, RF2-NEG.2, TP11.P$1, U2.2 (AGND), X9.3; also elsewhere on the board

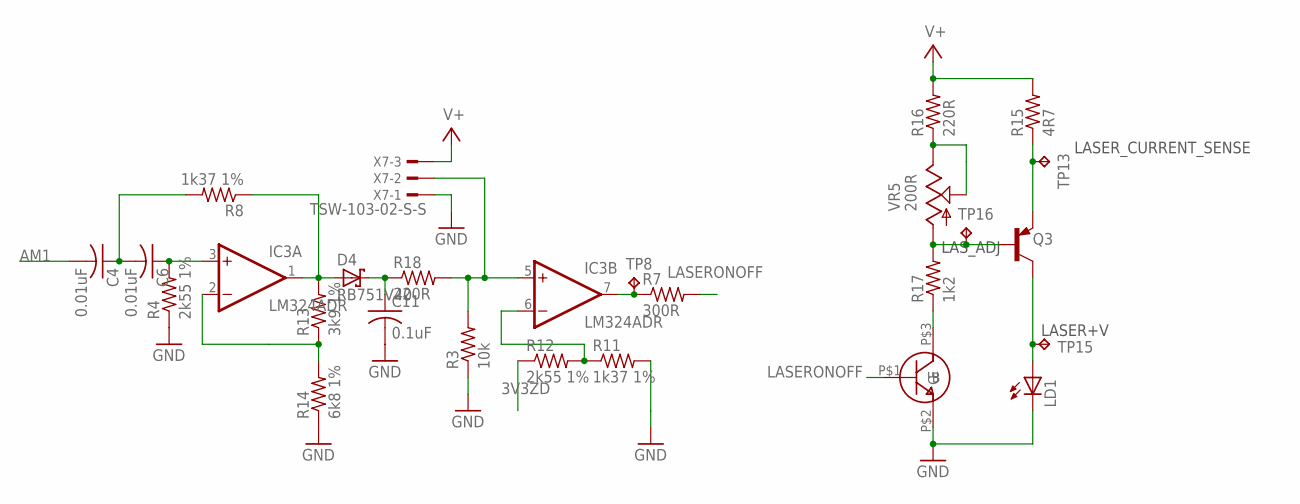
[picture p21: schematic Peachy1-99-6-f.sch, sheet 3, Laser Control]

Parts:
C4, C6: 0.01uF; C0805; MPN CL21B103KBANNNC
C11: 0.1uF; C0805; MPN CL21B104KACNNNC
D4: RB751V40; SOD323-R; MPN RB751V40,115
IC3: LM324ADR; SOIC14(TI-PKG-D); MPN LM324ADR
LD1: LASERDIODELD2; LASERDIODE2; MPN 3 x (0552-2-15-15-11-27-10-0)
Q3: BC857CT; SC-75
Q4: MMBT3904; SOT23; MPN MMBT3904,215
R3: 10k; R0805; MPN RMCF0805JT10K0
R4, R12: 2k55 1%; R0805; MPN RC0805FR-072K55L
R7: 300R; R0805; MPN RC0805JR-07300RL
R8, R11: 1k37 1%; R0805; MPN RC0805FR-071K37L
R13: 3k9 1%; R0805; MPN RC0805FR-073K9L
R14: 6k8 1%; R0805; MPN RC0805FR-076K8L
R15: 4R7; R0805; MPN RMCF0805JT4R70
R16, R18: 220R; R0805; MPN RMCF0805JT220R
R17: 1k2; R0805; MPN RC2012J122CS
TP8, TP13, TP15, TP16: TP017HOLE; TP017TH
VR5: 200R; TC33X; MPN ???
X7: TSW-103-02-S-S; MPN TSW-103-07-T-S

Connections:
3V3ZD: R12.1; also elsewhere on the board
AM1: C4.2; also elsewhere on the board
GND: C11.2, LD1.P$3 (C), Q4.P$2 (E), R3.1, R4.1, R11.2, R14.1, X7.1; also elsewhere on the board
LASERONOFF: Q4.P$1 (B), R7.2
unnamed: IC3.5 (+IN), R3.2, R18.2, X7.2
unnamed: IC3.6 (-IN), R11.1, R12.2
unnamed: IC3.2 (-IN), R13.1, R14.2
unnamed: LD1.P$1 (A), Q3.P$3 (C), TP15.P$1
unnamed: IC3.7 (OUT), R7.1, TP8.P$1
unnamed: C6.1, IC3.3 (+IN), R4.2
unnamed: C4.1, C6.2, R8.2
unnamed: D4.A, IC3.1 (OUT), R8.1, R13.2
unnamed: C11.1, D4.C, R18.1
unnamed: R16.1, VR5.P$2 (S), VR5.P$3 (E)
unnamed: Q3.P$1 (B), R17.2, TP16.P$1, VR5.P$1 (A)
unnamed: Q4.P$3 (C), R17.1
unnamed: Q3.P$2 (E), R15.1, TP13.P$1
V+: R15.2, R16.2, X7.3; also elsewhere on the board

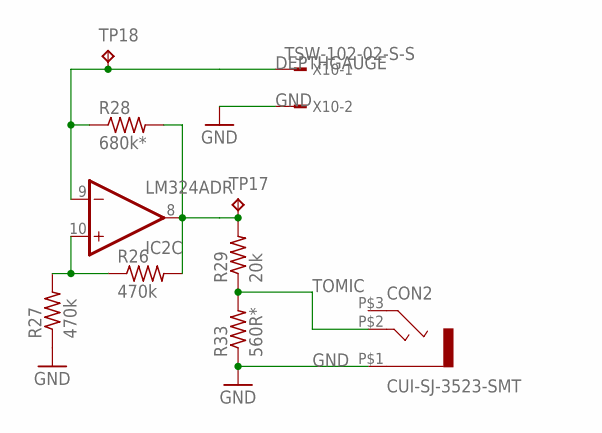
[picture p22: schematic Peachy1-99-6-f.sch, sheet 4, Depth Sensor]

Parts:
CON2: CUI-SJ-3523-SMT; MPN SJ-3523-SMT-TR
IC2: LM324ADR; SOIC14(TI-PKG-D); MPN LM324ADR
R26, R27: 470k; R0805; MPN RMCF0805JT470K
R28: 680k*; 70543-02; MPN PPTC021LFBN-RC
R29: 20k; R0805; MPN RMCF0805JT20K0
R33: 560R*; R0805; MPN RMCF0805JT560R
TP17, TP18: TP017HOLE; TP017TH
X10: TSW-102-02-S-S

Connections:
DEPTHGAUGE: IC2.9 (-IN), R28.1, TP18.P$1, X10.1
GND: CON2.P$1 (1), R27.1, R33.1, X10.2; also elsewhere on the board
unnamed: IC2.8 (OUT), R26.2, R28.2, R29.2, TP17.P$1
unnamed: IC2.10 (+IN), R26.1, R27.2
TOMIC: CON2.P$2 (3), R29.1, R33.2

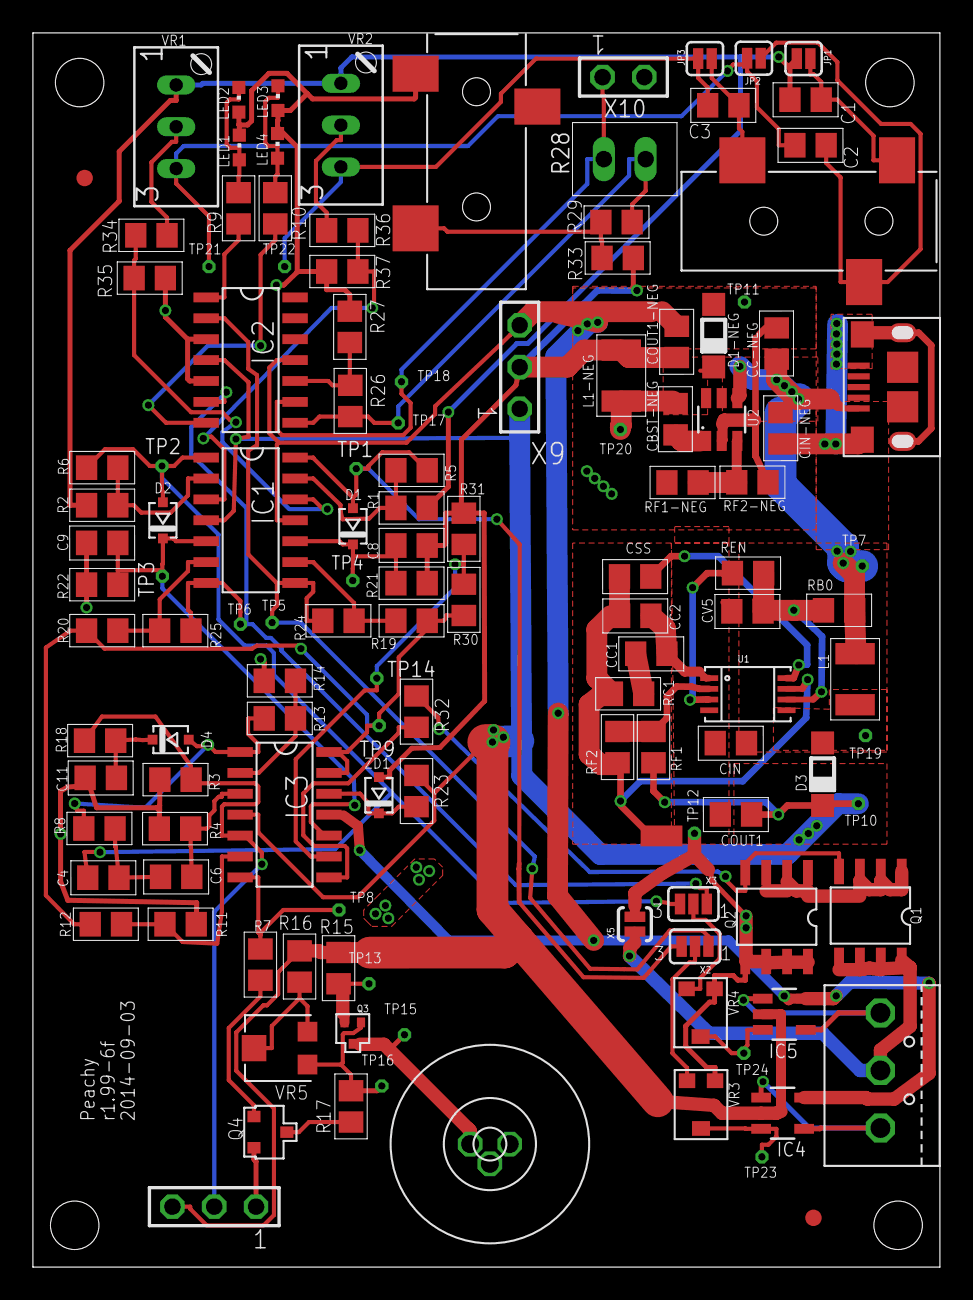
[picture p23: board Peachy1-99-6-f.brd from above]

Board: 2 copper layers, 55.1 x 75.0 mm, 131 parts (0 on the bottom side), 70 nets.

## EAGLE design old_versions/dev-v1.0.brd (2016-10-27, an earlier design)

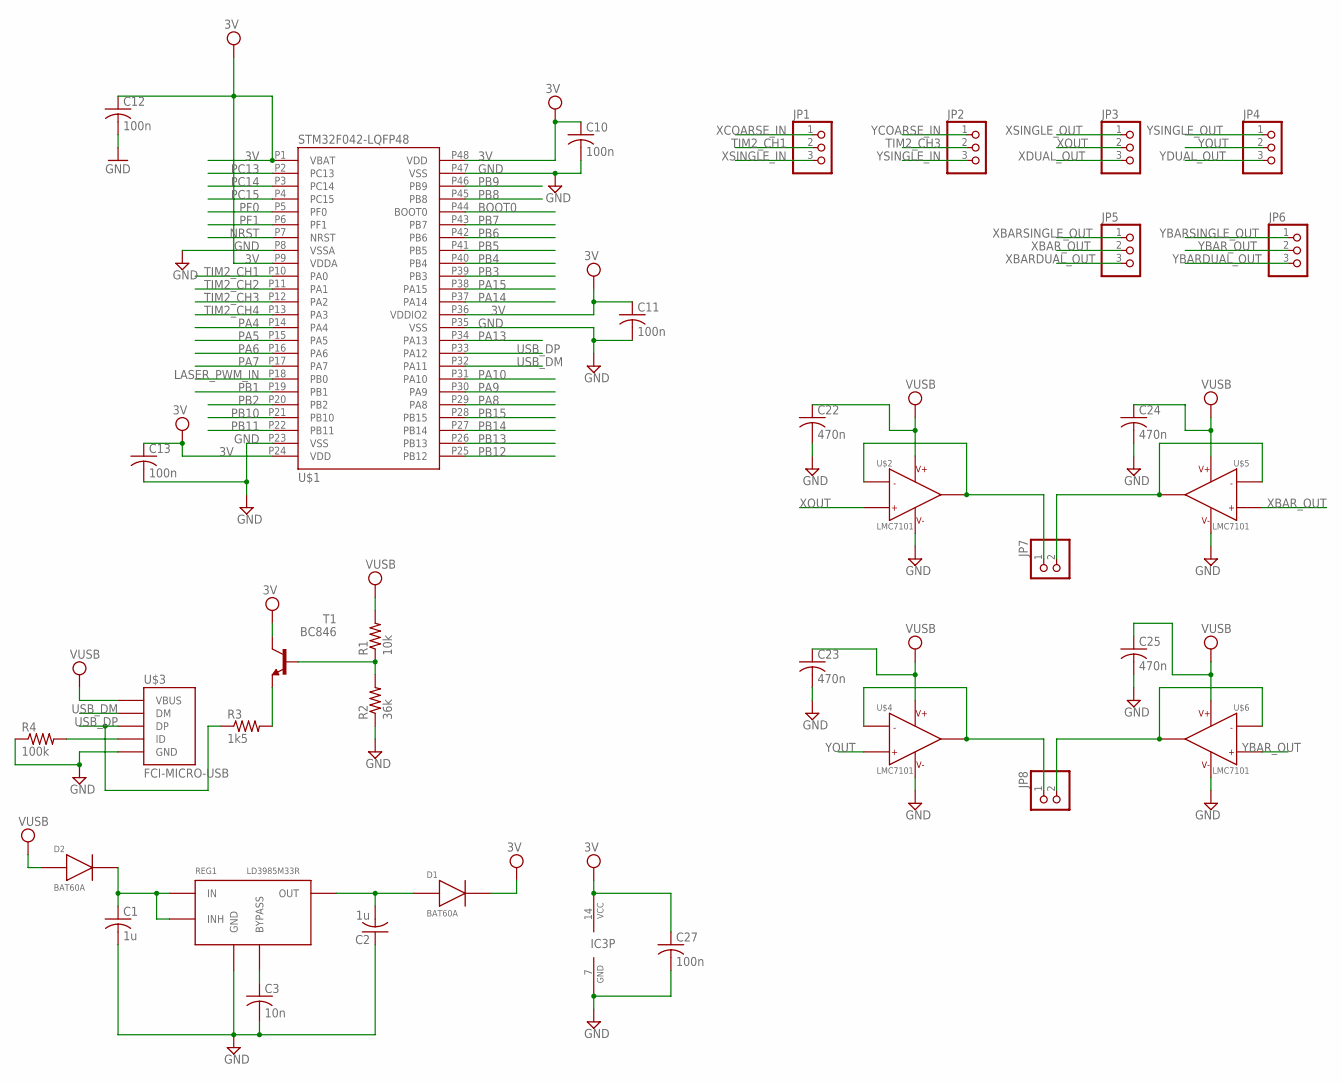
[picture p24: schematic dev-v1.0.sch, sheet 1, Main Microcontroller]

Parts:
C1, C2: 1u; C0603
C3: 10n; C0603
C10, C11, C12, C13, C27: 100n; C0603
C22, C23, C24, C25: 470n; C0603
D1, D2: BAT60A; SOD323
IC3: 74S04D; SO14
JP1, JP2, JP3, JP4, JP5, JP6: PINHD-1X3; 1X03
JP7, JP8: PINHD-1X2; 1X02
R1: 10k; R0603
R2: 36k; R0603
R3: 1k5; R0603
R4: 100k; R0603
REG1: LD3985M33R; SOT23-5L
T1: BC846; SOT23
U$1: STM32F042-LQFP48; LQFP48
U$2, U$4, U$5, U$6: LMC7101; SOT23-5
U$3: FCI-MICRO-USB; FCI-MICROUSB

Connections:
3V: C10.1, C11.1, C12.1, C13.1, C27.1, D1.1, IC3.14 (VCC), T1.3 (C), U$1.P1 (VBAT), U$1.P9 (VDDA), U$1.P24 (VDD), U$1.P36 (VDDIO2), U$1.P48 (VDD); also elsewhere on the board
3V3: C2.2, D1.2, REG1.OUT
BOOT0: U$1.P44 (BOOT0); also elsewhere on the board
GND: C1.2, C2.1, C3.2, C10.2, C11.2, C12.2, C13.2, C22.2, C23.2, C24.2, C25.2, C27.2, IC3.7 (GND), R2.1, R4.1, REG1.GND, U$1.P8 (VSSA), U$1.P23 (VSS), U$1.P35 (VSS), U$1.P47 (VSS), U$2.5, U$3.P5 (GND), U$4.5, U$5.5, U$6.5; also elsewhere on the board
LASER_PWM_IN: U$1.P18 (PB0); also elsewhere on the board
unnamed: C3.1, REG1.BYPASS
unnamed: R1.1, R2.2, T1.1 (B)
unnamed: R3.2, T1.2 (E)
unnamed: C1.1, D2.1, REG1.IN, REG1.INHIBIT (INH)
unnamed: R4.2, U$3.P4 (ID)
unnamed: JP7.1, U$2.1, U$2.4
unnamed: JP8.1, U$4.1, U$4.4
unnamed: JP7.2, U$5.1, U$5.4
unnamed: JP8.2, U$6.1, U$6.4
NRST: U$1.P7 (NRST); also elsewhere on the board
PA4: U$1.P14 (PA4); also elsewhere on the board
PA5: U$1.P15 (PA5); also elsewhere on the board
PA6: U$1.P16 (PA6); also elsewhere on the board
PA7: U$1.P17 (PA7); also elsewhere on the board
PA8: U$1.P29 (PA8); also elsewhere on the board
PA9: U$1.P30 (PA9); also elsewhere on the board
PA10: U$1.P31 (PA10); also elsewhere on the board
PA13: U$1.P34 (PA13); also elsewhere on the board
PA14: U$1.P37 (PA14); also elsewhere on the board
PA15: U$1.P38 (PA15); also elsewhere on the board
PB1: U$1.P19 (PB1); also elsewhere on the board
PB2: U$1.P20 (PB2); also elsewhere on the board
PB3: U$1.P39 (PB3); also elsewhere on the board
PB4: U$1.P40 (PB4); also elsewhere on the board
PB5: U$1.P41 (PB5); also elsewhere on the board
PB6: U$1.P42 (PB6); also elsewhere on the board
PB7: U$1.P43 (PB7); also elsewhere on the board
PB8: U$1.P45 (PB8); also elsewhere on the board
PB9: U$1.P46 (PB9); also elsewhere on the board
PB10: U$1.P21 (PB10); also elsewhere on the board
PB11: U$1.P22 (PB11); also elsewhere on the board
PB12: U$1.P25 (PB12); also elsewhere on the board
PB13: U$1.P26 (PB13); also elsewhere on the board
PB14: U$1.P27 (PB14); also elsewhere on the board
PB15: U$1.P28 (PB15); also elsewhere on the board
PC13: U$1.P2 (PC13); also elsewhere on the board
PC14: U$1.P3 (PC14); also elsewhere on the board
PC15: U$1.P4 (PC15); also elsewhere on the board
PF0: U$1.P5 (PF0); also elsewhere on the board
PF1: U$1.P6 (PF1); also elsewhere on the board
TIM2_CH1: JP1.2, U$1.P10 (PA0); also elsewhere on the board
TIM2_CH2: U$1.P11 (PA1); also elsewhere on the board
TIM2_CH3: JP2.2, U$1.P12 (PA2); also elsewhere on the board
TIM2_CH4: U$1.P13 (PA3); also elsewhere on the board
USB_DM: U$1.P32 (PA11), U$3.P2 (DM); also elsewhere on the board
USB_DP: R3.1, U$1.P33 (PA12), U$3.P3 (DP); also elsewhere on the board
VUSB: C22.1, C23.1, C24.1, C25.1, D2.2, R1.2, U$2.2, U$3.P1 (VBUS), U$4.2, U$5.2, U$6.2; also elsewhere on the board
XBARDUAL_OUT: JP5.3; also elsewhere on the board
XBARSINGLE_OUT: JP5.1; also elsewhere on the board
XBAR_OUT: JP5.2, U$5.3
XCOARSE_IN: JP1.1; also elsewhere on the board
XDUAL_OUT: JP3.3; also elsewhere on the board
XOUT: JP3.2, U$2.3
XSINGLE_IN: JP1.3; also elsewhere on the board
XSINGLE_OUT: JP3.1; also elsewhere on the board
YBARDUAL_OUT: JP6.3; also elsewhere on the board
YBARSINGLE_OUT: JP6.1; also elsewhere on the board
YBAR_OUT: JP6.2, U$6.3
YCOARSE_IN: JP2.1; also elsewhere on the board
YDUAL_OUT: JP4.3; also elsewhere on the board
YOUT: JP4.2, U$4.3
YSINGLE_IN: JP2.3; also elsewhere on the board
YSINGLE_OUT: JP4.1; also elsewhere on the board


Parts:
C14, C16, C18, C20: 1u; C0603
C15, C17, C19, C21: 0.1u; C0603
IC3: 74S04D; SO14
R17, R19, R21, R23: 8k2; R0603
R18, R20, R22, R24: 82k; R0603

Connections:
GND: C14.2, C15.2, C16.2, C17.2, C18.2, C19.2, C20.2, C21.2; also elsewhere on the board
unnamed: C14.1, R17.2, R18.1
unnamed: C16.1, R19.2, R20.1
unnamed: C18.1, R21.2, R22.1
unnamed: C20.1, R23.2, R24.1
XBARSINGLE_IN: IC3.2 (O), R21.1
XBARSINGLE_OUT: C19.1, R22.2; also elsewhere on the board
XSINGLE_IN: IC3.1 (I), R17.1; also elsewhere on the board
XSINGLE_OUT: C15.1, R18.2; also elsewhere on the board
YBARSINGLE_IN: IC3.4 (O), R23.1
YBARSINGLE_OUT: C21.1, R24.2; also elsewhere on the board
YSINGLE_IN: IC3.3 (I), R19.1; also elsewhere on the board
YSINGLE_OUT: C17.1, R20.2; also elsewhere on the board


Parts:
C4, C5, C6, C7: 4.7n; C0603
IC3: 74S04D; SO14
R5, R7, R9, R11: 3k9; R0603
R6, R8, R10, R12: 1M; R0603

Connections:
GND: C4.2, C5.2, C6.2, C7.2; also elsewhere on the board
unnamed: IC3.10 (O), R11.1
unnamed: IC3.12 (O), R12.1
unnamed: IC3.8 (O), R10.1
unnamed: IC3.6 (O), R9.1
XBARDUAL_OUT: C6.1, R9.2, R10.2; also elsewhere on the board
XCOARSE_IN: IC3.5 (I), R5.1; also elsewhere on the board
XDUAL_OUT: C4.1, R5.2, R6.2; also elsewhere on the board
XFINE_IN: IC3.9 (I), R6.1
YBARDUAL_OUT: C7.1, R11.2, R12.2; also elsewhere on the board
YCOARSE_IN: IC3.11 (I), R7.1; also elsewhere on the board
YDUAL_OUT: C5.1, R7.2, R8.2; also elsewhere on the board
YFINE_IN: IC3.13 (I), R8.1


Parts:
C8: 470p; C0603
C9: 820n; C0603
C26: 1u; C0603
JP9: PINHD-1X2; 1X02
Q1: IRLR3105TR; DPAK
R13: 1; R0603
R14, R25: 1k; R0603
R15: 100; R0603
R16: 9k9; R0603
U1: LMH6645MF; SOT23-5

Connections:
GND: C9.2, C26.2, R13.1, R25.1, U1.2 (V-); also elsewhere on the board
LASER_PWM_IN: R16.2; also elsewhere on the board
unnamed: JP9.2, Q1.4 (D)
unnamed: Q1.3 (S), R13.2, R14.2
unnamed: C8.2, R14.1, U1.4 (IN-)
unnamed: Q1.1 (G), R15.2
unnamed: C8.1, R15.1, U1.1 (OUT)
unnamed: C9.1, R16.1, R25.2, U1.3 (IN+)
VUSB: C26.1, JP9.1, U1.5 (V+); also elsewhere on the board


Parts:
JP10, JP11, JP12, JP13: PINHD-1X12; 1X12
JP14: PINHD-1X3; 1X03
JP15: PINHD-1X5; 1X05

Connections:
3V: JP10.1, JP10.9, JP11.12, JP12.1, JP13.1, JP14.1, JP15.1; also elsewhere on the board
BOOT0: JP12.5, JP14.2; also elsewhere on the board
GND: JP10.8, JP11.11, JP12.2, JP13.2, JP14.3, JP15.5; also elsewhere on the board
LASER_PWM_IN: JP11.6; also elsewhere on the board
NRST: JP10.7, JP15.2; also elsewhere on the board
PA4: JP11.2; also elsewhere on the board
PA5: JP11.3; also elsewhere on the board
PA6: JP11.4; also elsewhere on the board
PA7: JP11.5; also elsewhere on the board
PA8: JP13.8; also elsewhere on the board
PA9: JP13.7; also elsewhere on the board
PA10: JP13.6; also elsewhere on the board
PA13: JP13.3, JP15.3; also elsewhere on the board
PA14: JP12.12, JP15.4; also elsewhere on the board
PA15: JP12.11; also elsewhere on the board
PB1: JP11.7; also elsewhere on the board
PB2: JP11.8; also elsewhere on the board
PB3: JP12.10; also elsewhere on the board
PB4: JP12.9; also elsewhere on the board
PB5: JP12.8; also elsewhere on the board
PB6: JP12.7; also elsewhere on the board
PB7: JP12.6; also elsewhere on the board
PB8: JP12.4; also elsewhere on the board
PB9: JP12.3; also elsewhere on the board
PB10: JP11.9; also elsewhere on the board
PB11: JP11.10; also elsewhere on the board
PB12: JP13.12; also elsewhere on the board
PB13: JP13.11; also elsewhere on the board
PB14: JP13.10; also elsewhere on the board
PB15: JP13.9; also elsewhere on the board
PC13: JP10.2; also elsewhere on the board
PC14: JP10.3; also elsewhere on the board
PC15: JP10.4; also elsewhere on the board
PF0: JP10.5; also elsewhere on the board
PF1: JP10.6; also elsewhere on the board
TIM2_CH1: JP10.10; also elsewhere on the board
TIM2_CH2: JP10.11; also elsewhere on the board
TIM2_CH3: JP10.12; also elsewhere on the board
TIM2_CH4: JP11.1; also elsewhere on the board
USB_DM: JP13.5; also elsewhere on the board
USB_DP: JP13.4; also elsewhere on the board


Board: 2 copper layers, 64.0 x 90.2 mm, 80 parts (0 on the bottom side), 86 nets.

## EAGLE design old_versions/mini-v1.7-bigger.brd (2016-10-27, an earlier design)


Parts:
C1, C2: 1u; C0603
C3: 10n; C0603
C10, C11, C12, C13, C27: 100n; C0603
C22, C23, C24, C25: 470n; C0603
D1, D2: BAT60A; SOD323
IC3: 74S04D; SO14
JP7, JP8: PINHD-1X2; 1X02
L1: ferrite; C0603
LED1, LED2, LED3, LED4: LEDCHIP-LED0603; CHIP-LED0603
R2, R3, R20, R21: R-US_R0603; R0603
R4: 100k; R0603
REG1: LD3985M33R; SOT23-5L
U$1: STM32F042-LQFP48; LQFP48
U$2, U$4, U$5, U$6: LMC7101; SOT23-5
U$3: FCI-MICRO-USB; FCI-MICROUSB
U$10, U$13: MBR0520; SOD123
U$11, U$12: SP3002; SC70-6

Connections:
3V: C10.1, C11.1, C12.1, C13.1, C27.1, D1.1, IC3.14 (VCC), U$1.P1 (VBAT), U$1.P9 (VDDA), U$1.P24 (VDD), U$1.P36 (VDDIO2), U$1.P48 (VDD); also elsewhere on the board
3V3: C2.2, D1.2, REG1.OUT
ADC0: U$1.P10 (PA0); also elsewhere on the board
ADC1: U$1.P11 (PA1); also elsewhere on the board
ADC2: U$1.P12 (PA2); also elsewhere on the board
ADC3: U$1.P13 (PA3); also elsewhere on the board
BOOT0: U$1.P44 (BOOT0); also elsewhere on the board
GND: C1.2, C2.1, C3.2, C10.2, C11.2, C12.2, C13.2, C22.2, C23.2, C24.2, C25.2, C27.2, IC3.7 (GND), LED1.C, LED2.C, LED3.C, LED4.C, R4.1, REG1.GND, U$1.P8 (VSSA), U$1.P23 (VSS), U$1.P35 (VSS), U$1.P47 (VSS), U$2.5, U$3.P5 (GND), U$4.5, U$5.5, U$6.5, U$10.ANODE, U$11.P2 (GND), U$12.P2 (GND), U$13.ANODE; also elsewhere on the board
LASER_PWM_IN: U$1.P40 (PB4); also elsewhere on the board
MISO: U$1.P16 (PA6); also elsewhere on the board
MOSI: U$1.P17 (PA7); also elsewhere on the board
unnamed: C3.1, REG1.BYPASS
unnamed: R2.2, U$1.P25 (PB12)
unnamed: LED2.A, R2.1
unnamed: C1.1, D2.1, REG1.IN, REG1.INHIBIT (INH)
unnamed: R4.2, U$3.P4 (ID)
unnamed: JP7.1, U$2.1, U$2.4, U$11.P6 (IO4)
unnamed: JP8.1, U$4.1, U$4.4, U$11.P1 (IO1)
unnamed: LED1.A, R3.1
unnamed: R3.2, U$1.P26 (PB13)
unnamed: L1.2, U$3.P1 (VBUS)
unnamed: JP7.2, U$5.1, U$5.4, U$11.P4 (IO3)
unnamed: JP8.2, U$6.1, U$6.4, U$11.P3 (IO2)
unnamed: LED3.A, R20.1
unnamed: LED4.A, R21.1
unnamed: R20.2, U$1.P27 (PB14)
unnamed: R21.2, U$1.P28 (PB15)
NRST: U$1.P7 (NRST); also elsewhere on the board
SCK: U$1.P15 (PA5); also elsewhere on the board
SCL: U$1.P6 (PF1); also elsewhere on the board
SDA: U$1.P5 (PF0); also elsewhere on the board
SPI_CS: U$1.P18 (PB0); also elsewhere on the board
SWCLK: U$1.P37 (PA14); also elsewhere on the board
SWDIO: U$1.P34 (PA13); also elsewhere on the board
USB_DM: U$1.P32 (PA11), U$3.P2 (DM), U$12.P1 (IO1)
USB_DP: U$1.P33 (PA12), U$3.P3 (DP), U$12.P3 (IO2)
VUSB: C22.1, C23.1, C24.1, C25.1, D2.2, L1.1, U$2.2, U$4.2, U$5.2, U$6.2, U$10.CATHODE, U$11.P5 (VCC), U$12.P5 (VCC), U$13.CATHODE; also elsewhere on the board
XBARDUAL_OUT: U$5.3; also elsewhere on the board
XCOARSE_IN: U$1.P38 (PA15); also elsewhere on the board
XDUAL_OUT: U$2.3; also elsewhere on the board
XFINE_IN: U$1.P39 (PB3); also elsewhere on the board
YBARDUAL_OUT: U$6.3; also elsewhere on the board
YCOARSE_IN: U$1.P21 (PB10); also elsewhere on the board
YDUAL_OUT: U$4.3; also elsewhere on the board
YFINE_IN: U$1.P22 (PB11); also elsewhere on the board


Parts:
C4, C5, C6, C7: 4.7n; C0603
IC3: 74S04D; SO14
R5, R7, R9, R11: 3k9; R0603
R6, R8, R10, R12: 1M; R0603

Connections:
GND: C4.2, C5.2, C6.2, C7.2, IC3.1 (I), IC3.3 (I); also elsewhere on the board
unnamed: IC3.10 (O), R11.1
unnamed: IC3.12 (O), R12.1
unnamed: IC3.8 (O), R10.1
unnamed: IC3.6 (O), R9.1
XBARDUAL_OUT: C6.1, R9.2, R10.2; also elsewhere on the board
XCOARSE_IN: IC3.5 (I), R5.1; also elsewhere on the board
XDUAL_OUT: C4.1, R5.2, R6.2; also elsewhere on the board
XFINE_IN: IC3.9 (I), R6.1; also elsewhere on the board
YBARDUAL_OUT: C7.1, R11.2, R12.2; also elsewhere on the board
YCOARSE_IN: IC3.11 (I), R7.1; also elsewhere on the board
YDUAL_OUT: C5.1, R7.2, R8.2; also elsewhere on the board
YFINE_IN: IC3.13 (I), R8.1; also elsewhere on the board


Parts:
C8: 470p; C0603
C9: 820n; C0603
C14: 10uF; C0603
C15: 560pF/50V; C0603
C16: 2.2u; C0603
C26: 1u; C0603
LD1: LASERDIODELD2; LASERDIODE2; MPN 3 x (0552-2-15-15-11-27-10-0)
Q1: IRLR3105TR; DPAK
R13: 1; R0603
R14, R25: 1k; R0603
R15: 100; R0603
R16: 9k9; R0603
R17: 52k3; R0603
R18: 13k3; R0603
R19: 1M; R0603
U1: LMH6645MF; SOT23-5
U$8: LMR62014; SOT23-5
U$9: MBR0520; SOD123
U$14: SDR0403-100ML; SDR0403

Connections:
6V: C14.1, C15.2, C26.1, LD1.P$1 (A), R17.2, U1.5 (V+), U$9.CATHODE
GND: C9.2, C14.2, C16.2, C26.2, R13.1, R18.1, R25.1, U1.2 (V-), U$8.2 (GND); also elsewhere on the board
LASER_PWM_IN: R16.2; also elsewhere on the board
unnamed: U$8.1 (SW), U$9.ANODE, U$14.P$2
unnamed: LD1.P$3 (C), Q1.4 (D)
unnamed: Q1.3 (S), R13.2, R14.2
unnamed: C8.2, R14.1, U1.4 (IN-)
unnamed: Q1.1 (G), R15.2
unnamed: C8.1, R15.1, U1.1 (OUT)
unnamed: C9.1, R16.1, R25.2, U1.3 (IN+)
unnamed: C15.1, R17.1, R18.2, U$8.3 (FB)
unnamed: R19.2, U$8.4 (/SHDN)
VUSB: C16.1, R19.1, U$8.5 (VIN), U$14.P$1; also elsewhere on the board


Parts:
JP1: PINHD-2X8; 2X08
JP2: PINHD-2X2; 2X02
JP4: PINHD-1X2; 1X02
R1: 10k; R0603

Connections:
3V: JP1.1, JP1.2, JP4.1; also elsewhere on the board
ADC0: JP1.11; also elsewhere on the board
ADC1: JP1.13; also elsewhere on the board
ADC2: JP1.8; also elsewhere on the board
ADC3: JP1.10; also elsewhere on the board
BOOT0: JP4.2, R1.2; also elsewhere on the board
GND: JP1.12, JP1.14, JP1.15, JP1.16, JP2.4, R1.1; also elsewhere on the board
MISO: JP1.9; also elsewhere on the board
MOSI: JP1.7; also elsewhere on the board
NRST: JP2.1; also elsewhere on the board
SCK: JP1.5; also elsewhere on the board
SCL: JP1.4; also elsewhere on the board
SDA: JP1.6; also elsewhere on the board
SPI_CS: JP1.3; also elsewhere on the board
SWCLK: JP2.2; also elsewhere on the board
SWDIO: JP2.3; also elsewhere on the board


Board: 2 copper layers, 38.0 x 66.0 mm, 74 parts (0 on the bottom side), 59 nets.

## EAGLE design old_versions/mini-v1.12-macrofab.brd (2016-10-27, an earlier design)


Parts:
C1, C2: 1u; C0603
C10, C11, C12, C13: 100n; C0603
D2: BAT42; SOD323
J1: USB_MICRO_RIGHT; MICROUSB-RIGHT
L1: ferrite; C0603
LED1, LED2, LED3, LED4: LEDCHIP-LED0603; CHIP-LED0603
R2, R3, R20, R21: 2k; R0603
R4: 100k; R0603
R26: 604k; R0603
R35: 825k; R0603
U2: TLV70233PDBVR; SOT-23-5
U$1: STM32F042-LQFP48; LQFP48
U$10, U$13: SMF6.0A; SOD123
U$12: SP3002; SC70-6

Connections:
3V: C2.2, C10.1, C11.1, C12.1, C13.1, U2.P$5 (VOUT), U$1.P1 (VBAT), U$1.P9 (VDDA), U$1.P24 (VDD), U$1.P36 (VDDIO2), U$1.P48 (VDD); also elsewhere on the board
ADC0: U$1.P10 (PA0); also elsewhere on the board
ADC1: U$1.P11 (PA1); also elsewhere on the board
ADC2: U$1.P12 (PA2); also elsewhere on the board
ADC3: U$1.P13 (PA3); also elsewhere on the board
BOOT0: U$1.P44 (BOOT0); also elsewhere on the board
GND: C1.2, C2.1, C10.2, C11.2, C12.2, C13.2, J1.5 (GND), LED1.C, LED2.C, LED3.C, LED4.C, R4.1, R26.P$2, R35.P$1, U2.P$2 (GND/ADJ), U$1.P8 (VSSA), U$1.P23 (VSS), U$1.P35 (VSS), U$1.P47 (VSS), U$10.ANODE, U$12.P2 (GND), U$13.ANODE; also elsewhere on the board
LASER_PWM_IN: U$1.P40 (PB4); also elsewhere on the board
MISO: U$1.P16 (PA6); also elsewhere on the board
MOSI: U$1.P17 (PA7); also elsewhere on the board
unnamed: R2.2, U$1.P25 (PB12)
unnamed: LED2.A, R2.1
unnamed: C1.1, D2.1, R35.P$2, U2.P$1 (VIN), U2.P$3 (EN)
unnamed: J1.4 (ID), R4.2
unnamed: LED1.A, R3.1
unnamed: R3.2, U$1.P26 (PB13)
unnamed: J1.1 (5V), L1.2
unnamed: J1.S1 (SLD), J1.S2 (SLD), J1.S3 (SLD), J1.S4 (SLD), J1.S5 (SLD), J1.S6 (SLD), R26.P$1
unnamed: LED3.A, R20.1
unnamed: LED4.A, R21.1
unnamed: R20.2, U$1.P27 (PB14)
unnamed: R21.2, U$1.P28 (PB15)
NRST: U$1.P7 (NRST); also elsewhere on the board
SCK: U$1.P15 (PA5); also elsewhere on the board
SCL: U$1.P6 (PF1); also elsewhere on the board
SDA: U$1.P5 (PF0); also elsewhere on the board
SPI_CS: U$1.P18 (PB0); also elsewhere on the board
SWCLK: U$1.P37 (PA14); also elsewhere on the board
SWDIO: U$1.P34 (PA13); also elsewhere on the board
USB_DM: J1.2 (D-), U$1.P32 (PA11), U$12.P1 (IO1)
USB_DP: J1.3 (D+), U$1.P33 (PA12), U$12.P3 (IO2)
VUSB: D2.2, L1.1, U$10.CATHODE, U$12.P5 (VCC), U$13.CATHODE; also elsewhere on the board
XCOARSE_IN: U$1.P38 (PA15); also elsewhere on the board
XFINE_IN: U$1.P39 (PB3); also elsewhere on the board
YCOARSE_IN: U$1.P21 (PB10); also elsewhere on the board
YFINE_IN: U$1.P22 (PB11); also elsewhere on the board

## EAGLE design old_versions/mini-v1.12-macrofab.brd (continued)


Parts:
C4, C5, C6, C7: 1u; C0603
C19: 1uF; C0603
C20: 0.1uF; C0603
JP3: PINHD-2X3; 2X03
R5, R8, R9, R10, R22, R23, R27, R28, R29, R36, R37, R38: 2k; R0603
R6, R11, R12, R30, R31, R33, R39, R40: 825k; R0603
R24, R32, R34, R41: 604k; R0603
U$2, U$4: NC7WZ14P6X; SC70-6
U$7, U$15, U$16, U$17: LMC7101; SOT23-5

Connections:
3V: R9.2, R22.2, R28.2, R37.2, U$2.P5 (VCC), U$4.P5 (VCC); also elsewhere on the board
ADC0: JP3.5; also elsewhere on the board
ADC1: JP3.6; also elsewhere on the board
COARSE1: R8.1, U$2.P6 (Y1)
FINE1: R11.1, R12.1, U$2.P4 (Y2)
FINE3: R39.1, R40.1, U$4.P4 (Y2)
GND: C4.P$2, C5.P$2, C6.P$2, C7.P$2, C19.P$2, C20.P$2, R10.1, R23.1, R29.1, R38.1, U$2.P2 (GND), U$4.P2 (GND), U$7.5, U$15.5, U$16.5, U$17.5; also elsewhere on the board
unnamed: R36.1, U$4.P6 (Y1)
unnamed: R11.2, R12.2, R24.1
unnamed: C4.P$1, R8.2, R9.1, R10.2, R24.2, U$15.3
unnamed: R30.2, R33.2, R34.1
unnamed: R6.2, R31.2, R32.1
unnamed: C5.P$1, R27.2, R28.1, R29.2, R34.2, U$16.3
unnamed: R39.2, R40.2, R41.1
unnamed: C6.P$1, R36.2, R37.1, R38.2, R41.2, U$17.3
OUT: JP3.1, U$7.1, U$7.4
OUT1: JP3.2, U$15.1, U$15.4
OUT2: JP3.3, U$16.1, U$16.4
OUT3: JP3.4, U$17.1, U$17.4
VUSB: C19.P$1, C20.P$1, U$7.2, U$15.2, U$16.2, U$17.2; also elsewhere on the board
XCOARSE_IN: R5.1, U$2.P1 (A1); also elsewhere on the board
XFINE_IN: R6.1, R31.1, U$2.P3 (A2); also elsewhere on the board
XSUM: C7.P$1, R5.2, R22.1, R23.2, R32.2, U$7.3
YCOARSE_IN: R27.1, U$4.P1 (A1); also elsewhere on the board
YFINE_IN: R30.1, R33.1, U$4.P3 (A2); also elsewhere on the board


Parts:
C8, C18: 0.1u; C0603
C9, C17: 1u; C0603
C14: 10uF; C0603
C15: 560pF/50V; C0603
LD1: LASERDIODELD2; LASERDIODE2; MPN 3 x (0552-2-15-15-11-27-10-0)
R7: 2k; R0603
R13, R14, R15: 1k69; R0603
R16: 100; R0603
R17: 63k4; R0603
R18: 13k3; R0603
R19: 825k; R0603
R25: 10; R0603
U1: N-CHANNEL_FET_SOT-23-3; SOT-23-3
U$5: OPAMP-SINGLELMC7101; SOT23-5
U$8: LMR62014; SOT23-5
U$9: MBR0520; SOD123
U$14: SDR0403-100ML; SDR0403

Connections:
6V: C14.1, C15.2, LD1.P$1 (A), R17.2, U$5.2 (V+), U$9.CATHODE
GND: C8.P$2, C9.P$2, C14.2, C17.P$2, C18.P$2, R15.P$2, R18.1, R25.P$1, U$5.5 (V-), U$8.2 (GND); also elsewhere on the board
LASER_PWM_IN: R7.P$2; also elsewhere on the board
unnamed: R7.P$1, R13.P$2
unnamed: R13.P$1, R14.P$2
unnamed: C8.P$1, R14.P$1, R15.P$1, U$5.3 (IN+)
unnamed: U$8.1 (SW), U$9.ANODE, U$14.P$2
unnamed: LD1.P$3 (C), U1.P$3 (DRAIN)
unnamed: R25.P$2, U1.P$2 (SOURCE), U$5.4 (IN-)
unnamed: R16.P$2, U1.P$1 (GATE)
unnamed: R16.P$1, U$5.1 (OUT)
unnamed: C15.1, R17.1, R18.2, U$8.3 (FB)
unnamed: R19.2, U$8.4 (/SHDN)
VUSB: C9.P$1, C17.P$1, C18.P$1, R19.1, U$8.5 (VIN), U$14.P$1; also elsewhere on the board


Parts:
JP1, JP5, JP6: PINHD-2X3; 2X03
JP4: PINHD-1X2; 1X02
R1: 10k; R0603

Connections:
3V: JP1.1, JP4.1, JP5.1, JP6.1; also elsewhere on the board
ADC2: JP6.3; also elsewhere on the board
ADC3: JP6.5; also elsewhere on the board
BOOT0: JP4.2, R1.2; also elsewhere on the board
GND: JP1.6, JP5.6, JP6.6, R1.1; also elsewhere on the board
MISO: JP5.2; also elsewhere on the board
MOSI: JP5.4; also elsewhere on the board
NRST: JP1.4; also elsewhere on the board
SCK: JP5.3; also elsewhere on the board
SCL: JP6.4; also elsewhere on the board
SDA: JP6.2; also elsewhere on the board
SPI_CS: JP5.5; also elsewhere on the board
SWCLK: JP1.3; also elsewhere on the board
SWDIO: JP1.5; also elsewhere on the board
VUSB: JP1.2; also elsewhere on the board


Board: 2 copper layers, 38.0 x 66.0 mm, 88 parts (0 on the bottom side), 63 nets.

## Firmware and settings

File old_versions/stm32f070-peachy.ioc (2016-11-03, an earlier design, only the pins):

Mcu.UserName=STM32F070CBTx
PA0.Signal=ADC_IN0
PA1.Signal=ADC_IN1
PA11.Signal=USB_DM
PA12.Signal=USB_DP
PA13.Signal=SYS_SWDIO
PA14.Signal=SYS_SWCLK
PA2.Signal=ADC_IN2
PA3.Signal=ADC_IN3
PA4.GPIO_Label=SPI_CS
PA4.Signal=GPIO_Output
PA5.Signal=SPI1_SCK
PA6.Signal=SPI1_MISO
PA7.Signal=SPI1_MOSI
PB0.GPIO_Label=YCOARSE_IN
PB0.Signal=S_TIM3_CH3
PB1.GPIO_Label=YFINE_IN
PB1.Signal=S_TIM3_CH4
PB10.Signal=I2C2_SCL
PB11.Signal=I2C2_SDA
PB14.GPIO_Label=LASER_PWM_IN
PB14.Signal=S_TIM15_CH1
PB15.GPIO_Label=LASER_EN
PB15.Signal=GPIO_Output
PB4.GPIO_Label=XCOARSE_IN
PB4.Signal=S_TIM3_CH1
PB5.GPIO_Label=XFINE_IN
PB5.Signal=S_TIM3_CH2

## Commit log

2016-10-27 Git cleanup, moving old (useless?) files out of the way
    [3-3V swing output Pdis.xlsx, DRILEGEND.CFG, Peachy1-99-6-f.sch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]
2016-10-27 Updated Scotts audio board files with his latest
    [Peachy1-99-6-f-costing.ods, Peachy1-99-6-f.brd, Peachy1-99-6-f.sch]
2016-11-03 More organisation, re-added deleted eagle files -_- woops
    [Peachy Pro BOM for mini-v1.7.xlsx, mini-v1.14-macrofab BOM digikey Oct 26.csv, mini-v1.14-macrofab BOM digikey Oct 26.xlsx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]
